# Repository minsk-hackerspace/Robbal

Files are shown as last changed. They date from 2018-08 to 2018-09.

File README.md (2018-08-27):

Robbal
===

Схемы, чертежи, инструкции по сборке робота балансира Rabbal

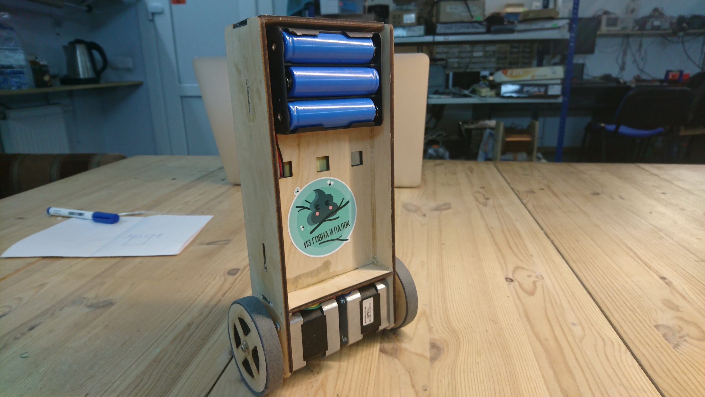
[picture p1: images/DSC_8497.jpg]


Робот баланси Robbal как отдельный [проект](https://hackerspace.by/projects/33) создается в рамках [курса](https://hackerspace.by/projects/31)

Купить готовый набор(конструктор) для сборки можно [в магазине Белчип](http://belchip.by/product/?selected_product=34442)

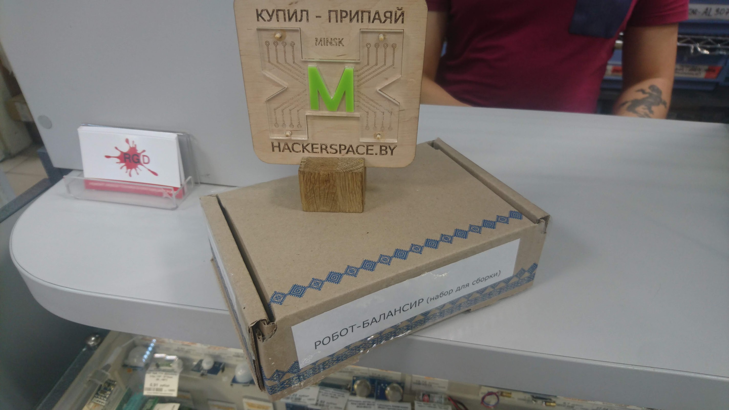
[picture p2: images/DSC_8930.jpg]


Основан на этом проекте [YABR](http://www.brokking.net/yabr_main.html)
Имеет более простую схему, а так-же управляется по блютусу с любого Android телефона.

Видео
---

ROBBAL (https://www.youtube.com/watch?v=0WFv116GKos)

Набор, Конструкция, Схема, Чертеж, Прошивка.
---

- [Комплектация набора](https://github.com/minsk-hackerspace/Robbal/blob/master/set.md)

- [Конструкция робота](https://github.com/minsk-hackerspace/Robbal/blob/master/design.md)

- [Схема робота](https://github.com/minsk-hackerspace/Robbal/blob/master/Robbal.png)

- [Чертеж корпуса](https://github.com/minsk-hackerspace/Robbal/blob/master/chassis.svg)

- [Скетч для Arduino](https://github.com/minsk-hackerspace/Robbal/blob/master/robbal/robbal.ino)

Инструкция по сборке:
---

- [блок питания](https://github.com/minsk-hackerspace/Robbal/blob/master/power.md)

- [шасси/корпус](https://github.com/minsk-hackerspace/Robbal/blob/master/chassis.md)

- [сборка схемы](https://github.com/minsk-hackerspace/Robbal/blob/master/assemble.md)

- [прошивка и нсатройка](https://github.com/minsk-hackerspace/Robbal/blob/master/tune.md)

- [найтройка bluetooth](https://github.com/minsk-hackerspace/Robbal/blob/master/bt.md)

- управление через android

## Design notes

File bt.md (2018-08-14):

Настройка bluetooth модуля HC-05
===

Управление роботом
---

Управление роботом осуществляется по bluetooth.
В качестве контроллера будет выступать любой Android смартфон с программой
Программа можете быть любая которая позволяет посылать настраиваеые команды на bloototh
В Play Market таких великое множество, например:

- [Arduino RC](https://play.google.com/store/apps/details?id=eu.jahnestacado.arduinorc)

- [Gadget Controller](https://play.google.com/store/apps/details?id=com.krio.gadgetcontroller)

Приемником управления будет выступать блютус модуль HC-05
Он позволит принять ваши команды управления из Андроид сматрфона и отдать их в ардуино робота.

Подключение для настройки
---

Блютус модуль в наборе поставляется в виде распространенного модуля HC-05 и переходной платки.
Платка позволяет втыкать его в макетку и питать от напряжения 5в (хотя логические уровни по прежнему остаются 3.3 вольта)
Так же на плате есть кнопка позволяющая перевести модуль в режим AT команд, зачем описано ниже.

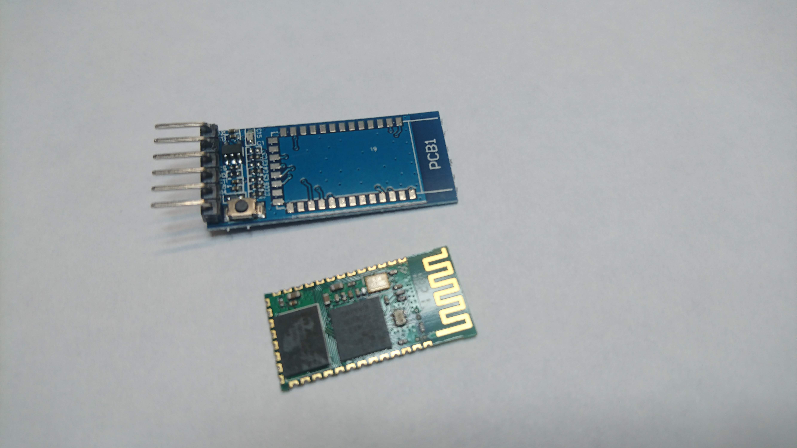
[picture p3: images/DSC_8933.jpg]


Модуль необходимо припапять на плату вот таким вот образом:
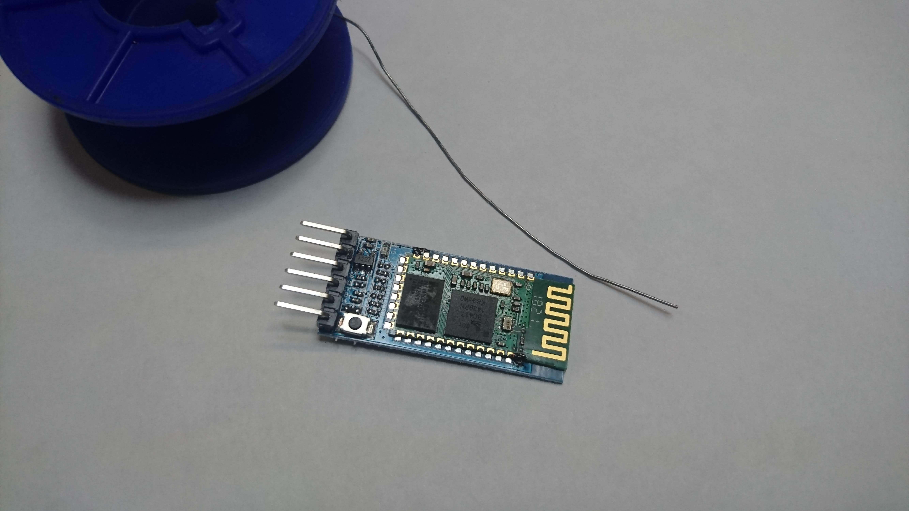
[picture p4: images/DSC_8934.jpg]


Должно получится что-то такое:
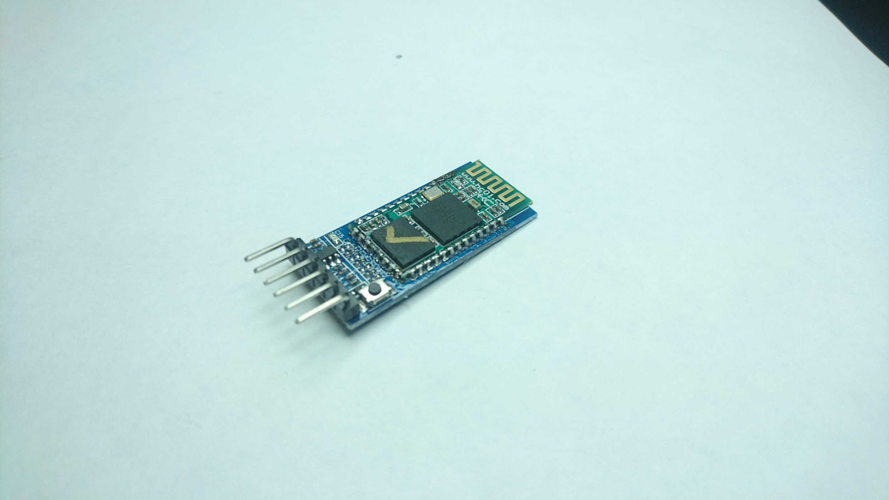
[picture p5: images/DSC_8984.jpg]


Далее необходимо настроить модуль под свои нужны. Все модули по дефолту имеют одинаковое имя и пароль, а так-же дефолтная скорость всего 9600 бод.

Для того чтобы настроить модуль, он подсоединяется через любой USB-UART переходник к компьютеру с Ardiono IDE. Важно джамперм или переключателем выставить напряжение UART 3.3 вольта.

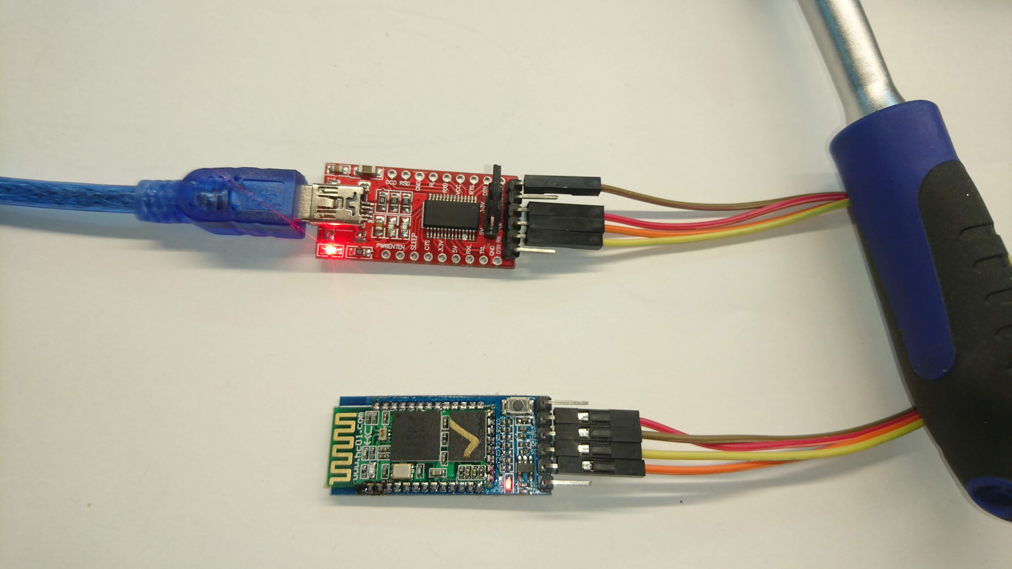
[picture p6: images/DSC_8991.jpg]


Подключение такое:

UART | HC-05
--- | ---
GND | GND
VCC | +5v
TX | RX
RX | TX

Настройка
---

Настройка происходит через Arduino IDE - Serial Monitor (Монитор порта) 
В строку ввода пишутся AT команды, а модуль как-то на них отвечает.
Чтобы зайти в AT режим необходимо подключать модуль с нажатой кнопкой на переходной платке.
В Serial Monitor необзодимо выставить скорость 38400 и перевод строки Both NL & CR (это стандартно для AT режима) 

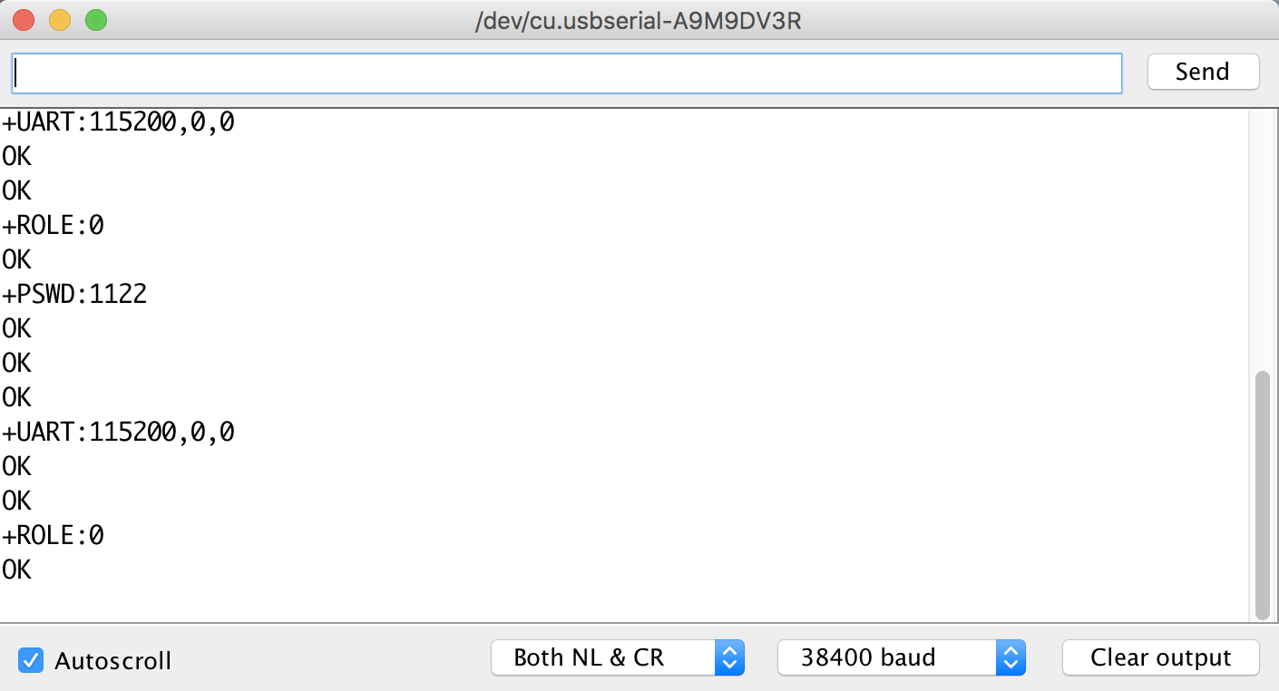
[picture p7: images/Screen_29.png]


Команда | Значение
--- | ---
AT | пустой запрос ответом должен быть OK
AT+NAME? | спросить имя модуля
AT+NAME=Robbal | задать имя модуля Robbal
AT+PSWD? | спросить пин код
AT+PSWD="1122" | Задать пин код 1122
AT+UART=115200,0,0 | Задать скорость уарт 115200 бод
AT+RESET | перезагрузка и выход из AT режима

Примерный листинг (лог) команд которым настраивается модуль с запросами и ответами.
```
> AT
< OK
> AT+NAME?
< +NAME:HC-05
> AT+NAME=Robbal
< OK
> AT+NAME?
< +NAME:Robbal
> AT+PSWD?
< +PIN:"1234"
> AT+PSWD="1122"
< OK
> AT+PSWD?
< +PIN:"1122"
> AT+ROLE?
< +ROLE:0
> AT+UART?
< +UART:9600,0,0
> AT+UART=115200,0,0
< OK
> AT+UART?
< +UART:115200,0,0
> AT+RESET
< OK
```

- [Полный мануал/даташит по модулю HC-05](http://www.electronicaestudio.com/docs/istd016A.pdf)

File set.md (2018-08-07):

Комплектация
===

[Набор](http://belchip.by/product/?selected_product=34442) для сборки из челчипа обладает минимальной комплектацией позволяющей собрать робота в хакерспейсе.

Название | модель/код | Количество
--- | --- | ---
Шаговый двигатель | 17HS2408 NEMA17 | 2	
Драйвер двигателя | Module DRV8825 | 2	
Аккумулятор 18650 | LIR18650 3.7V 2600mAh | 3	
Батарейный отсек | BH-3x18650 / 18650 x3 с проводами | 1	
Arduino Pro Mini | Модуль Atmega328 3В 8MHZ | 1
Модуль гироскопа | GY-521 MPU-6050 | 1
Модуль DC-DC | MP1584EN Mini | 1
Модуль Bluetooth | HC-05 Bluetooth Module | 1
Плата для Bluetooth | Base board for HC-05 | 1	

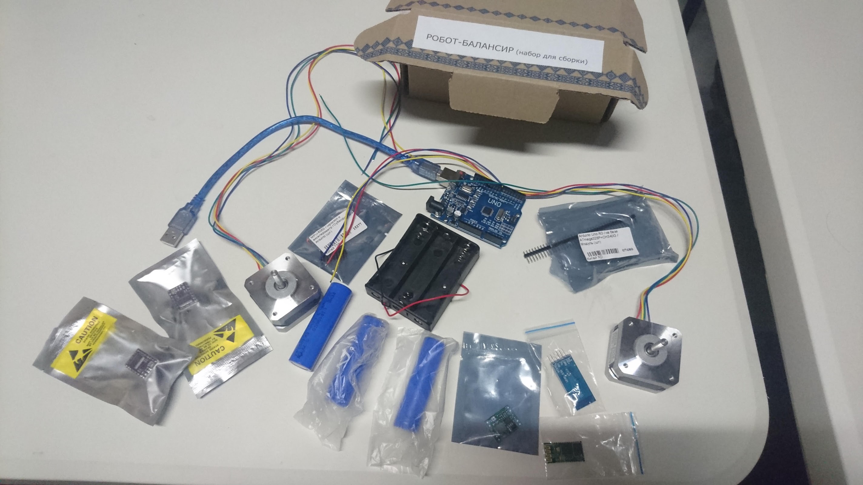
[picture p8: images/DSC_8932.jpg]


В комплект не входит необходимое для сборки и наладки:

- Переходник UART-USB для программирования Arduino 

- Зарядное устройство для аккумуляторов 18650

- Материал для корпуса / шасси / колес

Все это есть в хакерспейсе, но при самостоятельной сборке дома необходимо иметь ввиду.

Так же комплект можно расширить дополнительными деталями позволяющими расширить функциональность робота например:

- переключатель чтобы включать/выключать робота

- вольтметр чтобы отслеживать разряд батарей

- светодиодную ленту для подсветки

- сервопривод для механизма вставания

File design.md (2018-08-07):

Конструкция и дизайн робота
===

Робот разрабатывался для удовлетворения основных целей:

- простота конструкции и сборки

- минимальная и относительно дешевая комплектация

- широкие возможности для изменений/апгрейдов

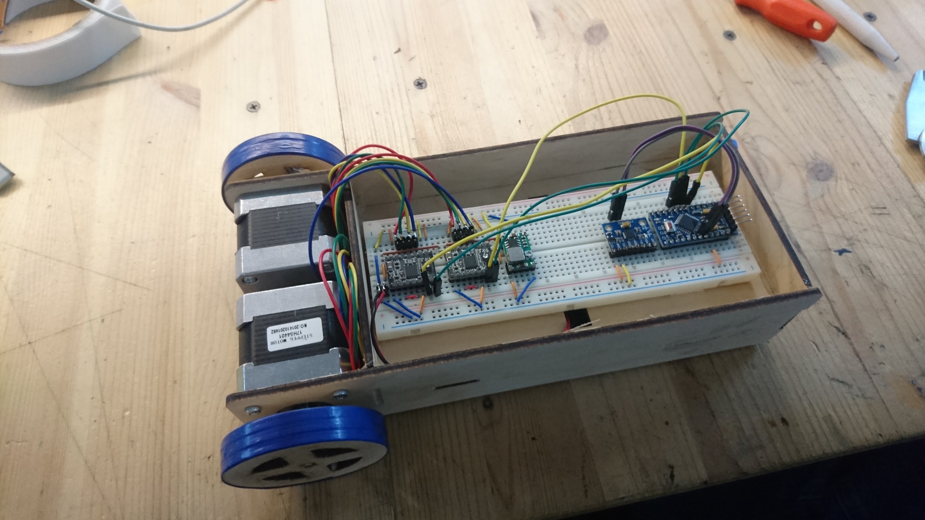
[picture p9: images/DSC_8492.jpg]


Физика и механка робота
---

В роботе вместо простых асинхронных используются более дорогие шаговые двигатели. Это обусловлено простотой настройки, высокой мощностью и точностью работы. Их не нужно будет согласовывать между собой, им не нужны редукторы, просто вставил и поехал. Можно использовать любые шаговики расчитанные на ток до 1.5 А. Корпус сделан под типоразмер NEMA17 но можно использовать более мощные NEMA23.

Корпус расчитан под лазерную резку минимального формата, но при этом позволяет разместить внутри стандартную макетную плату либо большую печатку размерами до 120х170. Так же копсус имеет два отдельных отсека что позволяет разместить схему и батарейки по разные стороны от оси, тем самым обеспечить более правильную балансировку по весу.

_При сборке робота для более качественной работы пид контроллера стоит размещать аккумуляторы в самой верхней части._

Конструкция робота позволяет менять ее в довольно широких пределах.
---

Есть несколько возможных вариантов сделать корпус, например:
- _корпус вырезанный из листового материала фанеры или акрила_ самый быстрый и проверенный способ. Раскрой для этого - [курпус в формате svg](https://rawgit.com/minsk-hackerspace/Robbal/master/chassis.svg). Необходимые размеры материала 30х40см, толщина 3-4мм
- _корпус напечатанный на 3д принтере_ самый сложный, долгий но самый крутой вариант. Необходимо самостоятельно моделировать и печатать корпус.

Есть несколько возможных вариантов собрать схему, например:

- _на контактной макетной плате_ самый быстрый, но самый ненадежный вариант детальки при падениях постоянно вываливаются. (макетка не входит в комплект)

- _паять на печатной макетке_  самый надежный но при этом самый трудоемкий вариант (печатка в комплект не входит)

- _навесной монтаж_ компромиссный вариант - просто проводками спаивать узлы между собой, затем на термоклей цеплять внутрь корпуса.

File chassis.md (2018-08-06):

ШАССИ
===

Шасси (корпус) вырезается лазером из фанеры (акрила) толщиной 3-4мм
Необходимая площадь листа для всех деталей корпуса 300х400мм

- [курпус в формате svg](https://rawgit.com/minsk-hackerspace/Robbal/master/chassis.svg)

- [курпус в формате dwg](https://rawgit.com/minsk-hackerspace/Robbal/master/chassis.dxf)

Нюансы
---
Пазы расчитаны под материал толщиной ровно 4 мм, поэтому если используется более тонкий матерал остаются щели, это нормально.

Внутренная полость достаточно большая (176х112 мм) чтобы туда поместилась стандартная беспаечная макетка, либо достаточно большая двухсторонная паечная макетка. 

Корпус сделан с минимальным клиренсом, так что при падении колеса поднимаются на пару миллиметров.

Колеса так же вырезаются из материала и на них натягивается колечко из резины (старая шина) Либо можно купить любые другие колеса для RC моделей диаметром 64-68 мм. Есть очень распространенные пластмассовые желтые и дешевые, ищутся по запросу "68mm robot wheel"

Сборка
---

Процесс сборки на фотках ниже.

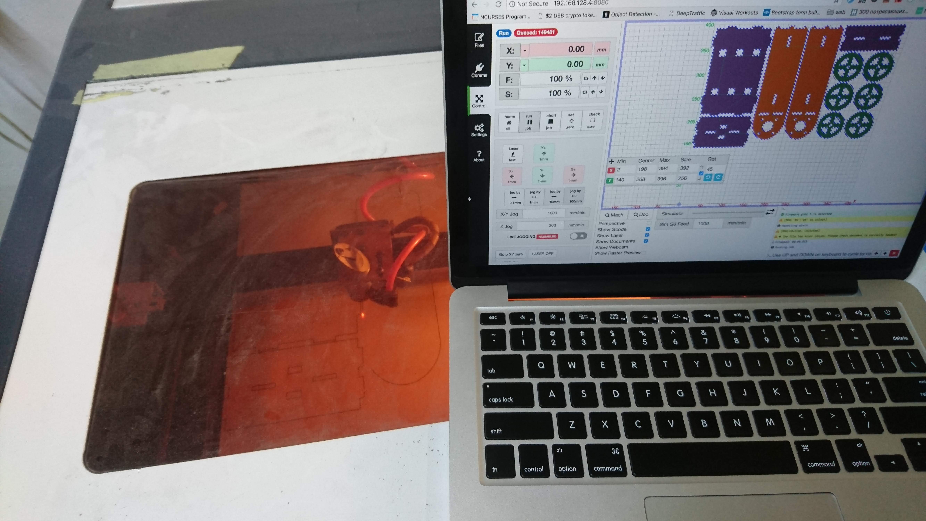
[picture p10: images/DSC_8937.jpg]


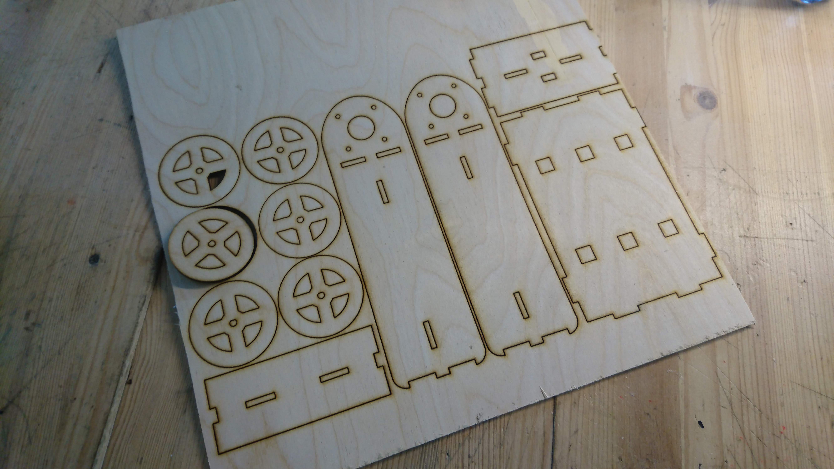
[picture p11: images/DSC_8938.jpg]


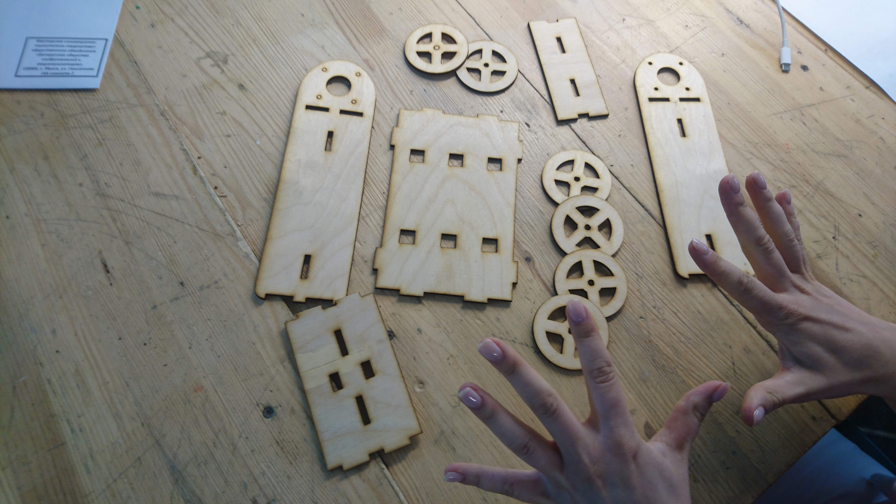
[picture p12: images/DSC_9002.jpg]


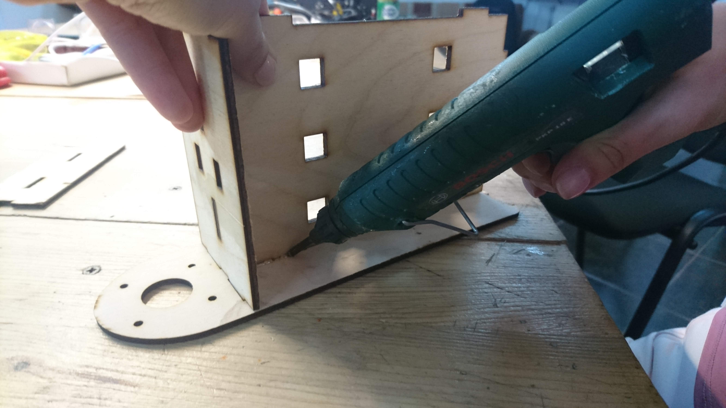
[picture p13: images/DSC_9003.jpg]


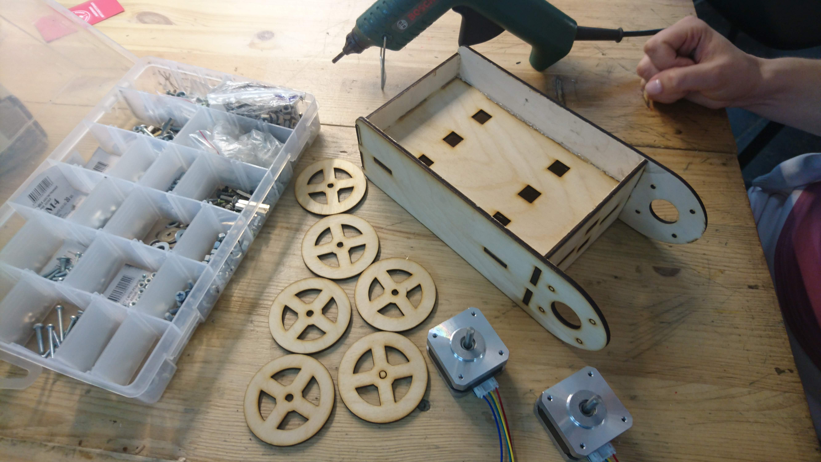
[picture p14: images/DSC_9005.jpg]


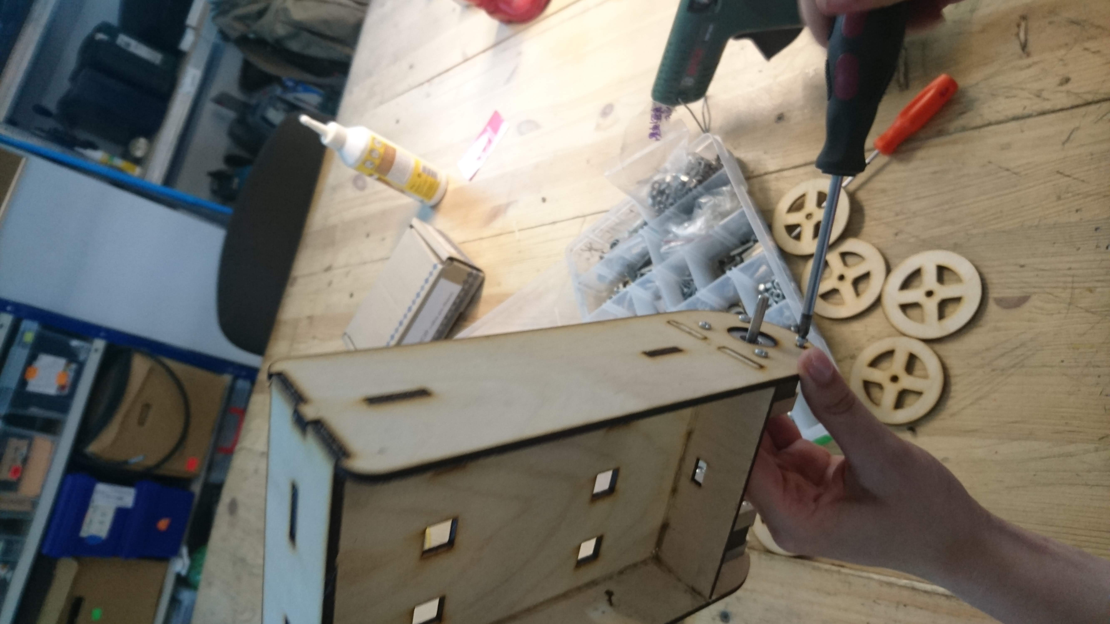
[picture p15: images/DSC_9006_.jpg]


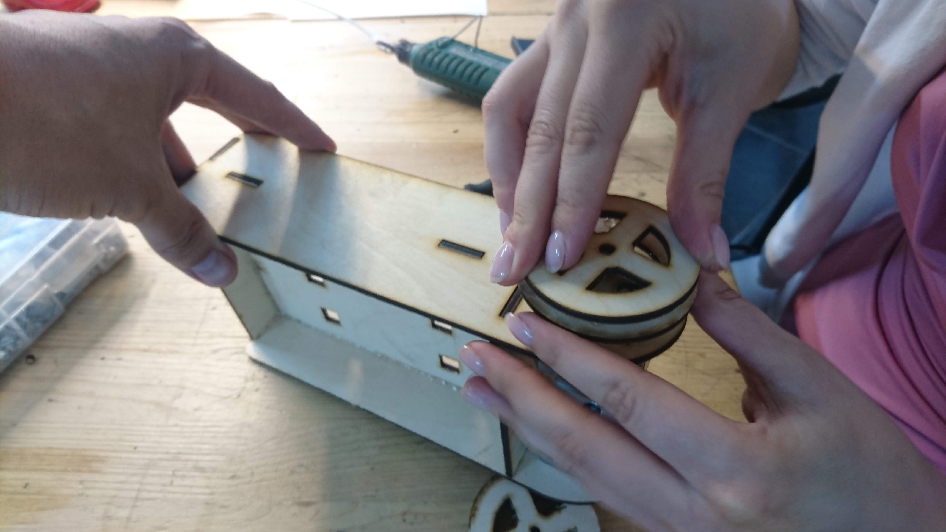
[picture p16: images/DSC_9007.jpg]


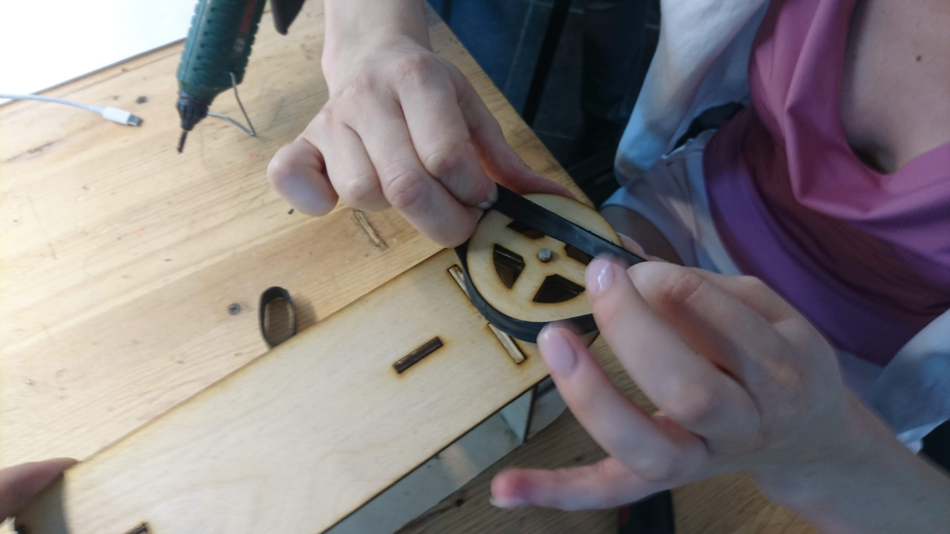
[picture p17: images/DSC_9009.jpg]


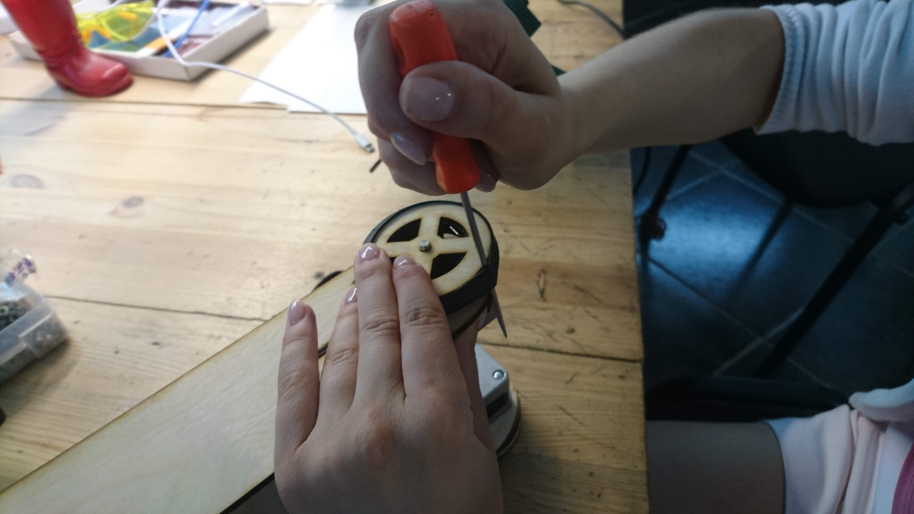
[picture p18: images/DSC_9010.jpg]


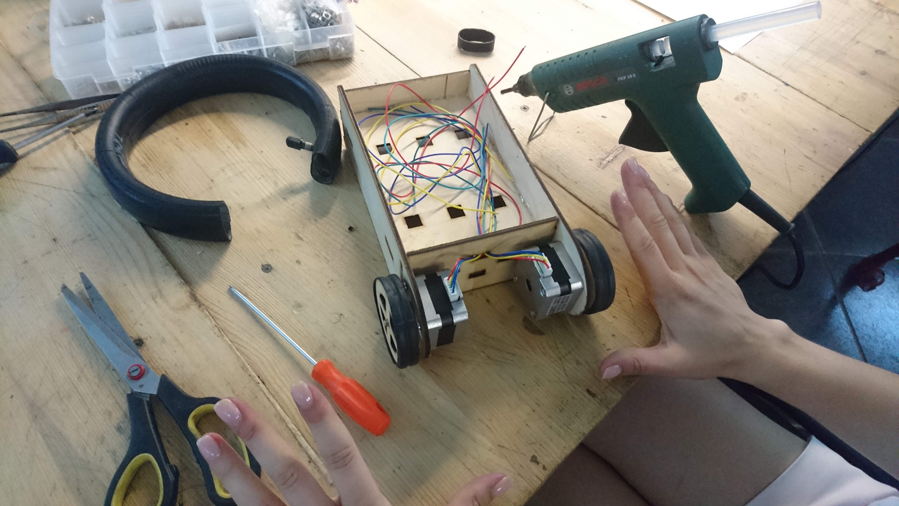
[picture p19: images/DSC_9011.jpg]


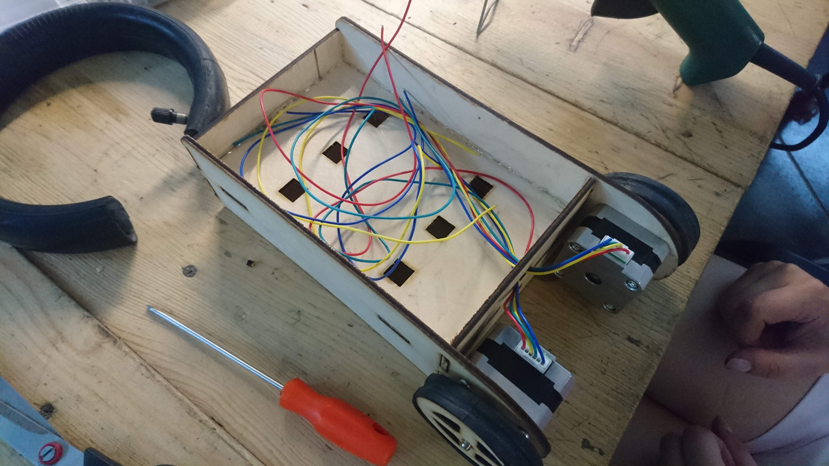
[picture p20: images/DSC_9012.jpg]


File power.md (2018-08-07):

Блок питания
===

Для питания роботу необходимы стабилизированные 3.3 вольта при токе до 100мА и нестабильные 9-24в с током до 1А для питания двигателей. Блок питания - это часть котоая будет выполнять эту функцию, состоит из:

- 3х Аккамулятор типоразмера 18650

- Акамуляторный отсек

- модуль преобразователя напряжения DC/DC 

Опционально в этот блок можно добавить выключатель и вольтметр.

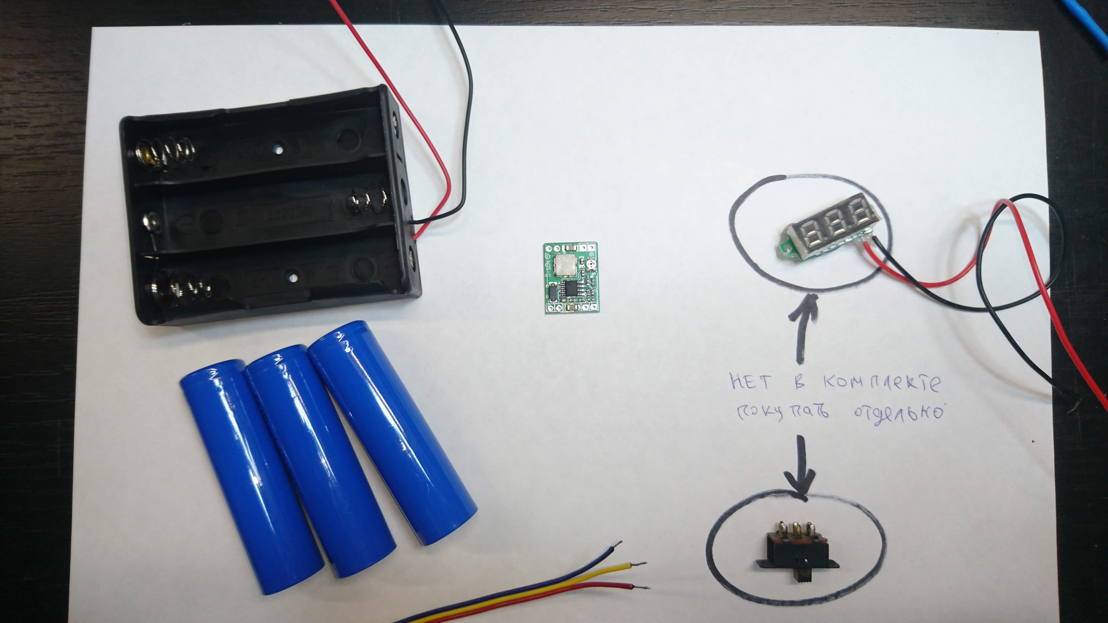
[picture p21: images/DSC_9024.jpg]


Схема
---

На общей схеме БП находится в левой верхней чертверти схемы.

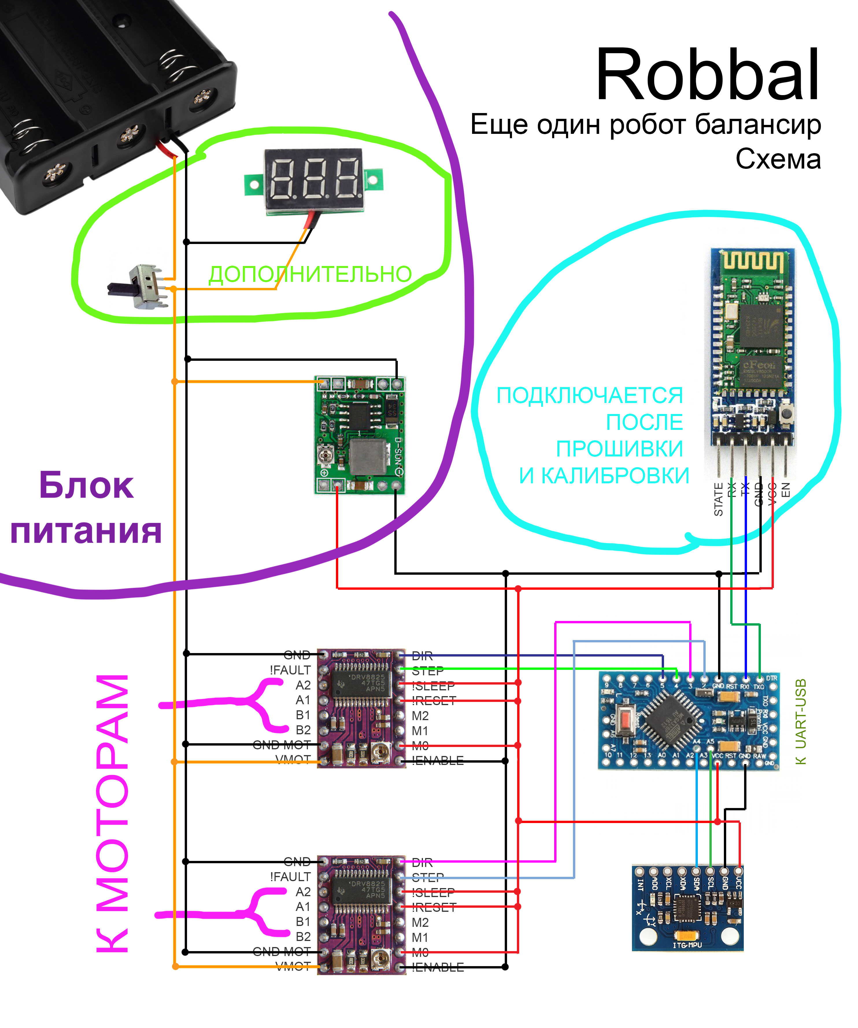
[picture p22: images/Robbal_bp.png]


Сборка
---

Фото процесса сборки: просто спайка проводами и крепление на термоклей

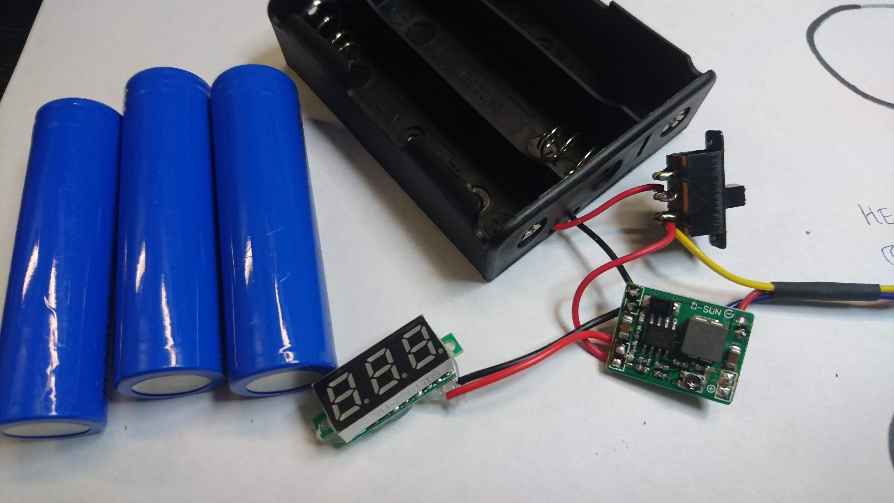
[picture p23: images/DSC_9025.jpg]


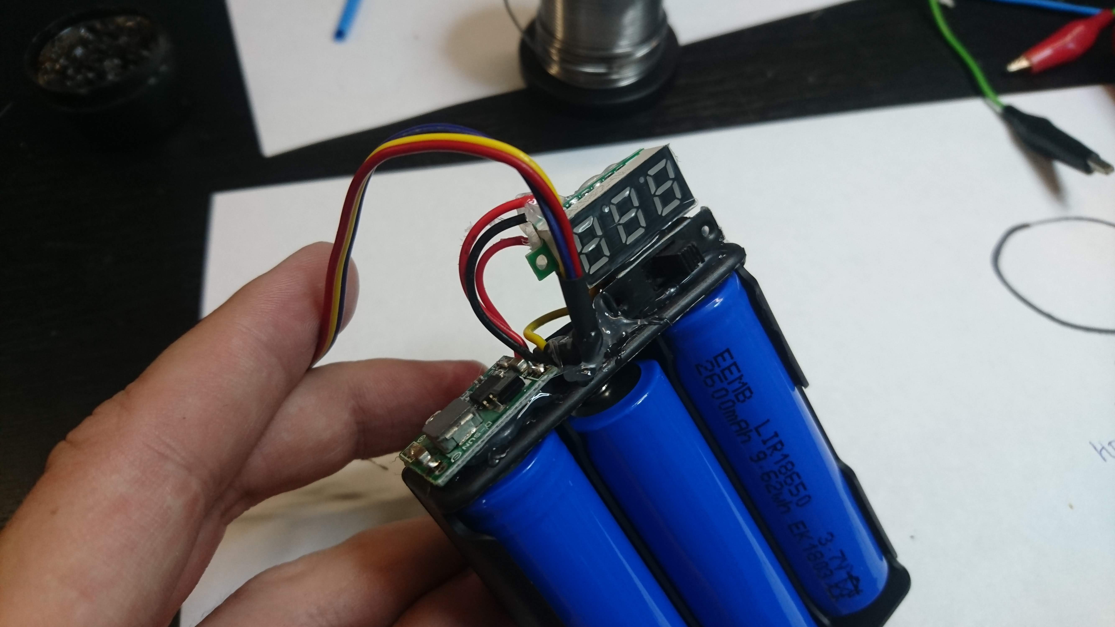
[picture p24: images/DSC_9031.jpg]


После сборки необходимо подкрутить подстроечный резистор на модуле DC/DC чтобы получить стабильное напряжение 3.3 В

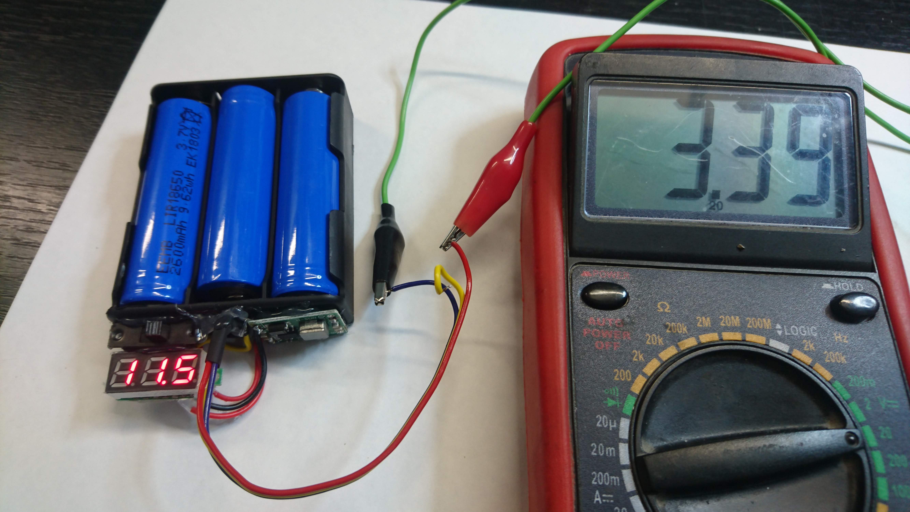
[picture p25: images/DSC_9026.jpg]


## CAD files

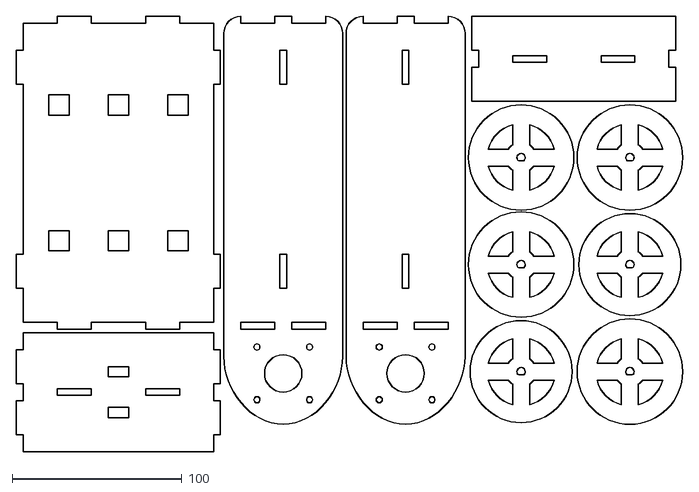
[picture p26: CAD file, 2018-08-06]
chassis.dxf
392.0 x 256.0

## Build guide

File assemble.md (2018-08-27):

СБОРКА СХЕМЫ
===

Схема условно делится на несколько частей:

* Блок питания 
* Основная схема 
* Блок управления



Схему можно собирать несколькими разными способами:

- Собрать на бесконтактной макетке

- Спаять на печатной макетной плате 

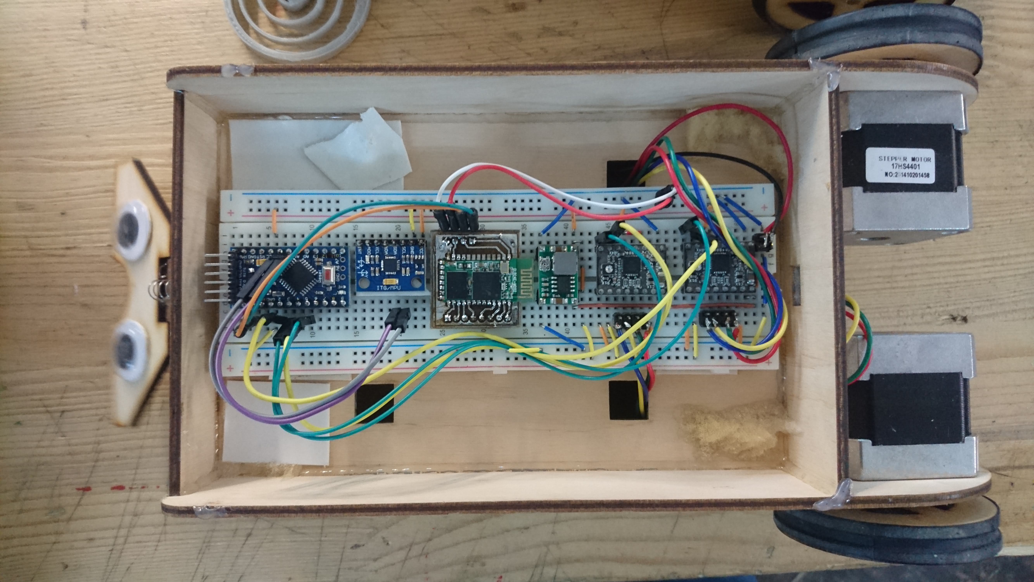
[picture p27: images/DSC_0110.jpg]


- Спаять модули проводами с некоторыми раззъемными соединениями

Сборка последним способом показанв на картинках ниже.

Сборка блока питания:
---

Блок питания это отсек с аккумуляторами и DC-DC преобразователь. Опционально можно добавить выключатель и модуль вольтметра чтобы видеть когда пора заряжать аккумуляторы. После спайки обязательно отрегулировать DC-DC модуль на стабилизированные +3.3В.
Так же сам DC-DC и дополнительные кнопку и вольтметр кремятся с помощью термопистолета на отсек.

В результате сборки блока питания зз него должно выходить три(четыре) провода:

- Нестабилизированные +11.7 В для питания двигателей. 
- Стабилизированные +3.3В для питания всей логики. 
- Земля одна или два провода.









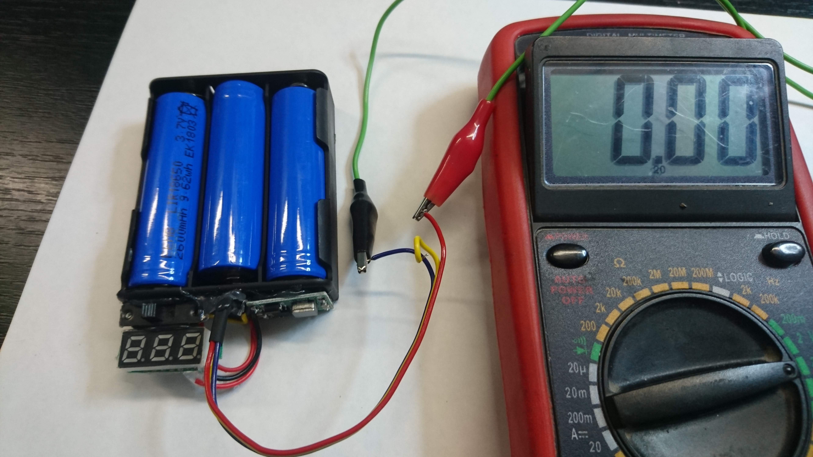
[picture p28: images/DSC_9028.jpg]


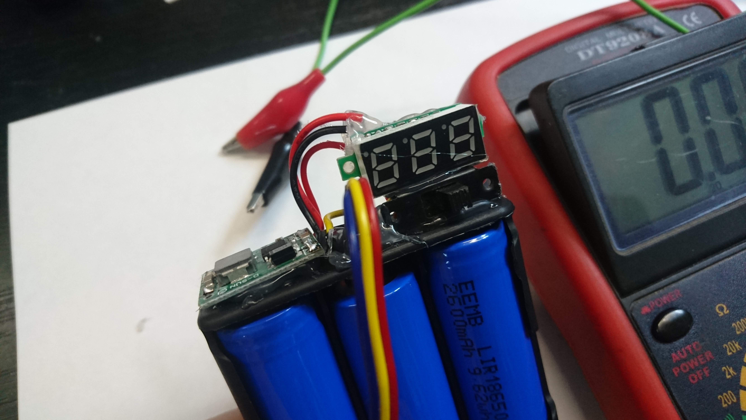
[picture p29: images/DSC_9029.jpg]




Сборка основной схемы:
---

Основная схема это соедененные проводами Ардуина, шаговые драйвера и гироскоп.
Соединяется все по схеме достаточно просто с помощью небольшого количества проводков.
Для удобства немлохо иметь коннекторы к шаговым двигателям и на питание всей схемы. 

Из нюансов стоит обратить внимание и правильно подсоединить к драйверам пары обмоток шагового двигателя. 
На фотографиях обмотки это синий+желтый и красный+зеленый.

Так же можно предусмотреть перемычки для настройки микростеппинга на драйверах. Хорошо себя показали 1/2 и 1/4 микрошага.
При 1/2 можно развить большую скорость. При 1/4 движения более плавные, робот легче в настройке и меньше падает.

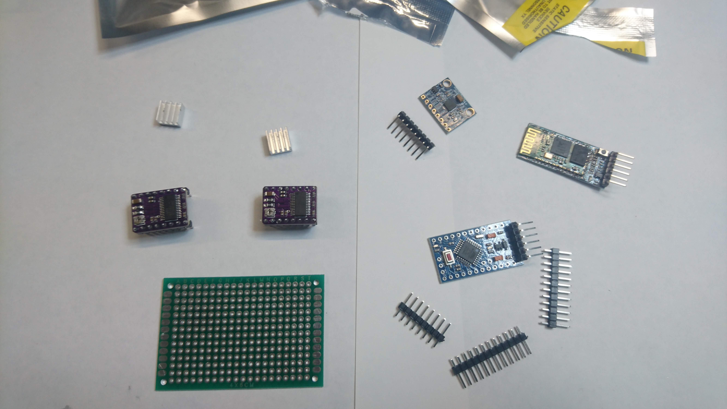
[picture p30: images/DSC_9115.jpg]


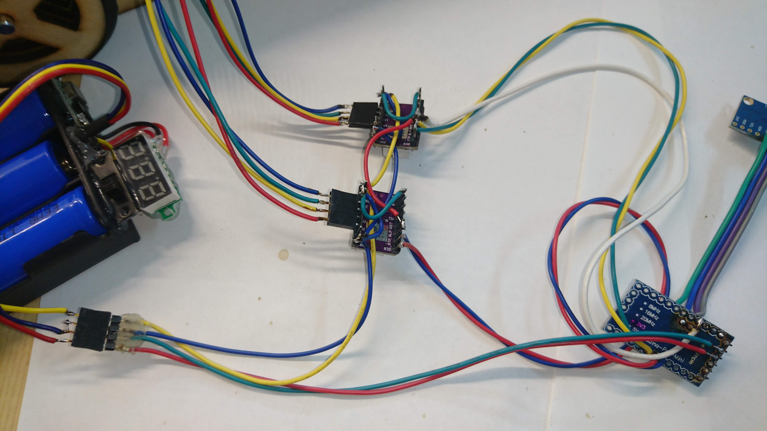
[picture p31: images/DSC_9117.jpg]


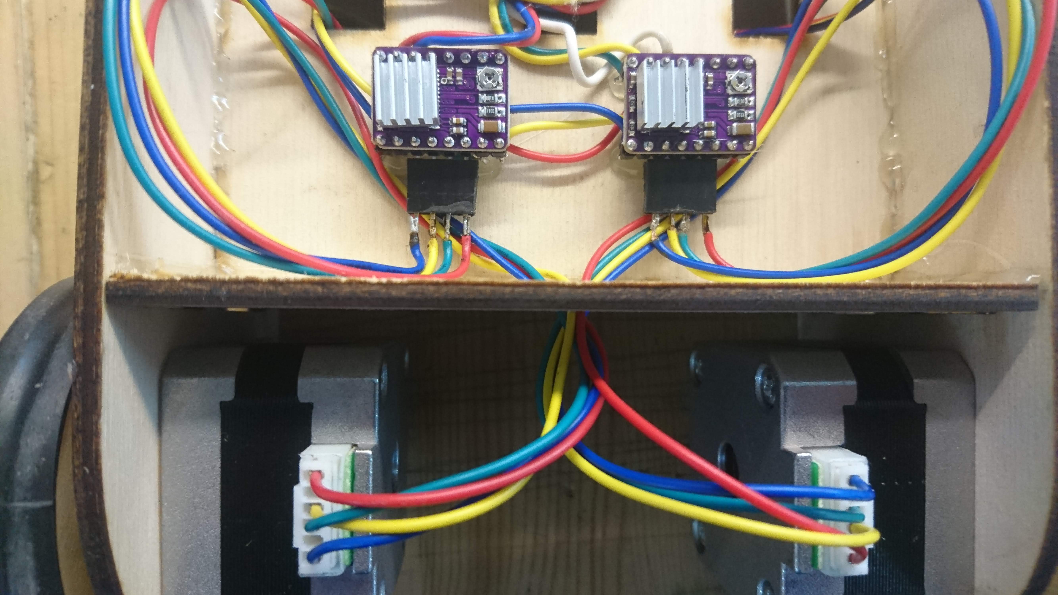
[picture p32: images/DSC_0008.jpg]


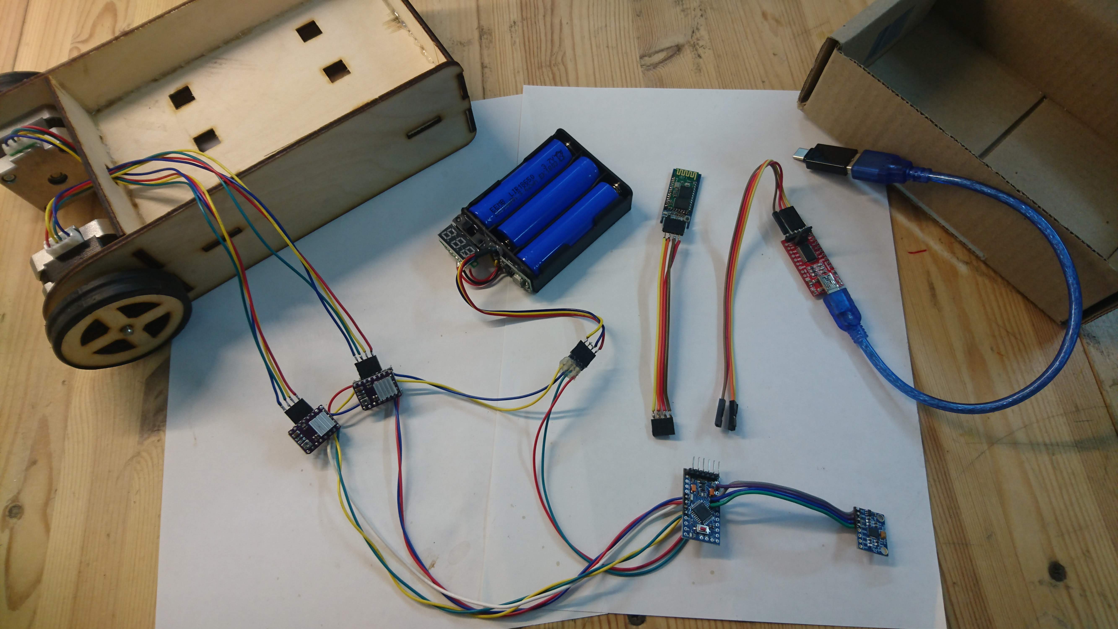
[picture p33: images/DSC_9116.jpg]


Сборка блока управления:
---

Блок управления - это модуль HC-05 распаяный на переходную платку. 
Так же удобно к нему иметь 4х жильный провод мама-мама чтобы подсоединять его напрямую к разъему на Arduino.
Подсоединяется он туда только после того [блютус модуль настроен](https://github.com/minsk-hackerspace/Robbal/blob/master/bt.md), а сама [схема откалибрована](https://github.com/minsk-hackerspace/Robbal/blob/master/tune.md)



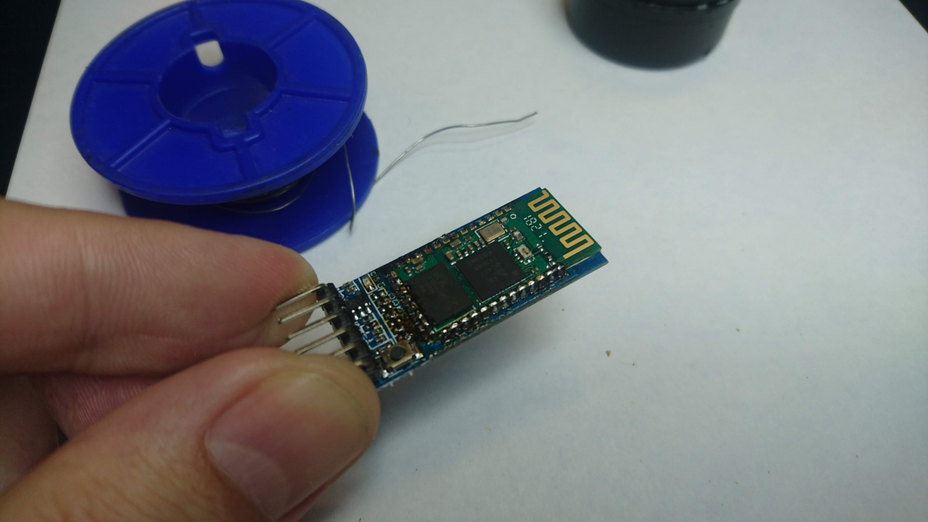
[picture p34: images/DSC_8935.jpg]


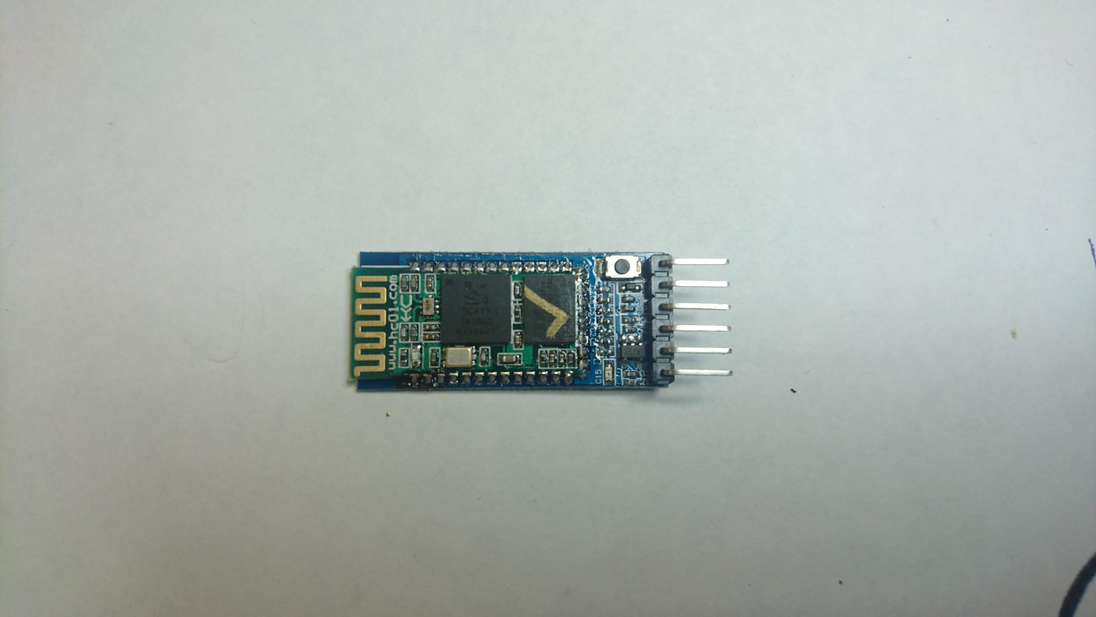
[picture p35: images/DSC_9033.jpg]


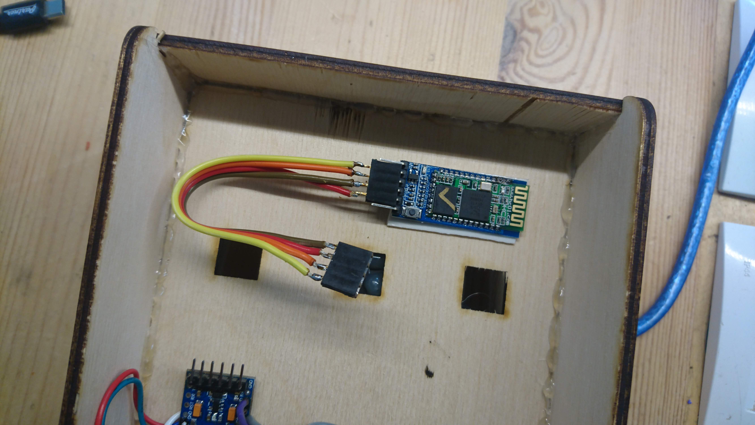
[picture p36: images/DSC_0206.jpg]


Крепление схемы в корпус
---
После спайки соединенные проводами модули крепится на термоклей внутрь корпуса.

*ВАЖНО* Разместить ось гироскопа таким образом чтобы версикальной была либо ось Y либо ось X. 
Маркировку осей можно увидеть на самом гироскопе.

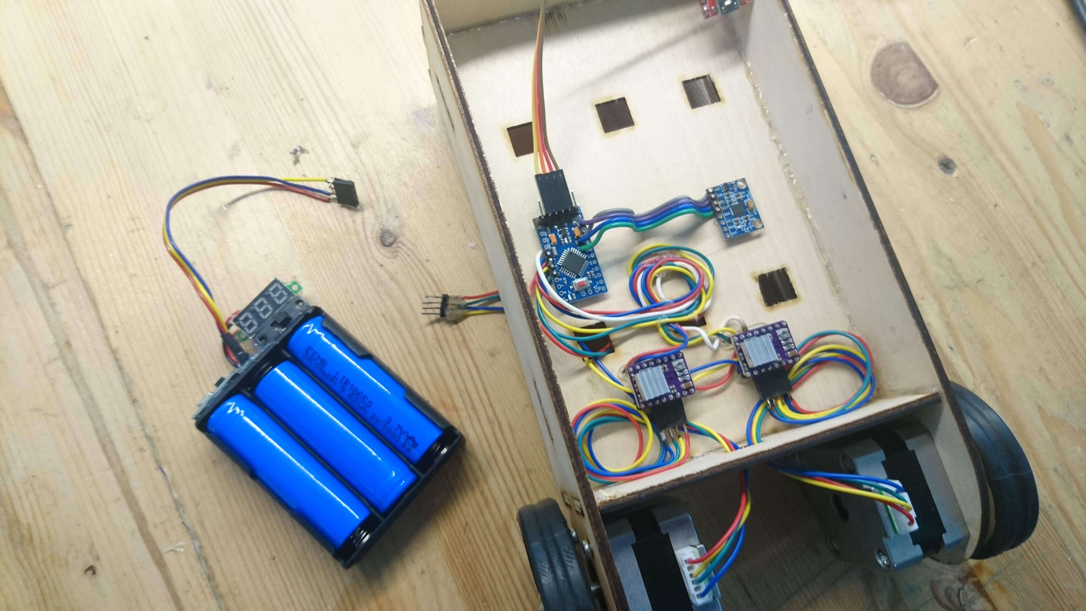
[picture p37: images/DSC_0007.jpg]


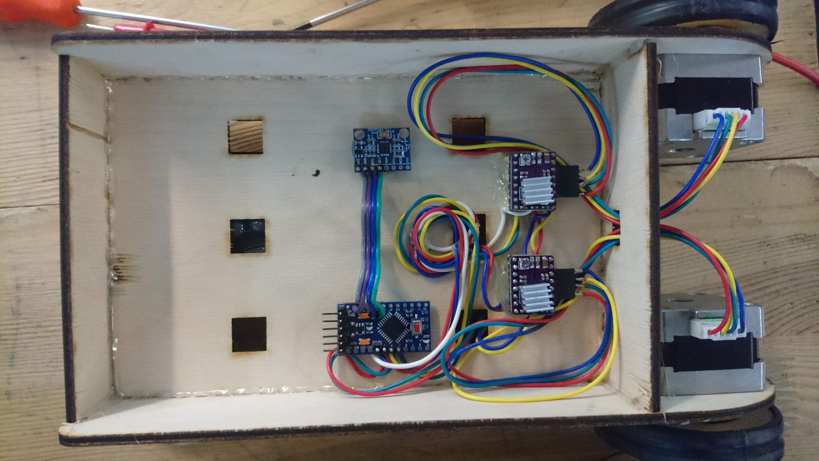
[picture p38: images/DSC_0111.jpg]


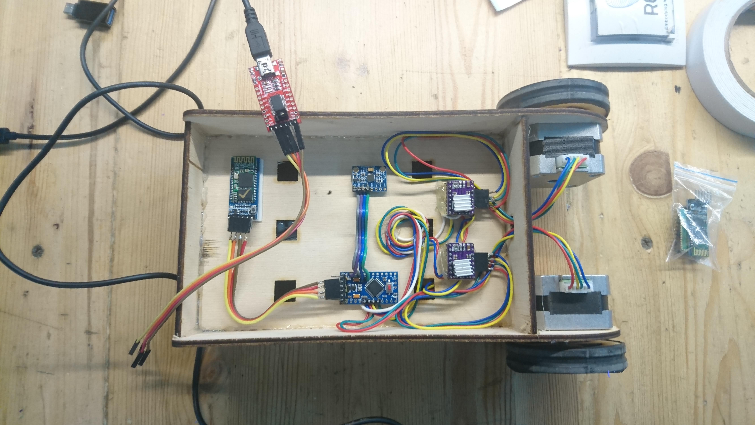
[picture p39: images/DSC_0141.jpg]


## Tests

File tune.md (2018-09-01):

Прошивка, настройка и калибровка.
===

Настройка драйверов.
---

Первым делом после сборки схемы необходимо выставить ограничение тока шаговых двигателей.
Это делается при первом включении. Проще всего это сделать при помощи измерения напряжения на подстроечном резисторе, которым собственно и ограничивается ток. Формула для драйвера DRV8825 такая: ``` Imax = 2 * Vref ```
Если используются шаговые двигатели с током обмоток 0.6А, то подстроечный резистор необходимо накрутить так, чтобы на нем было напряжение 0.3В

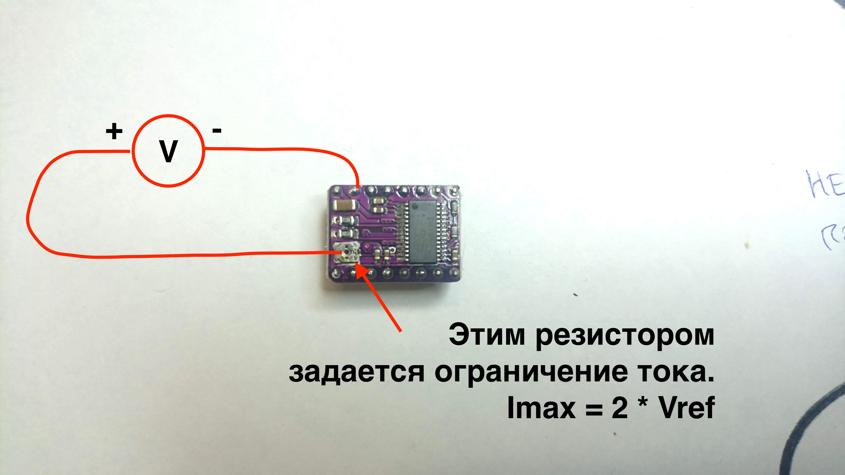
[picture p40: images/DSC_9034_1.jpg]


Более подробная стастья по настройке [тут](https://www.pololu.com/product/1182)

Прошивка.
---

В прошивке Arduino нет ничего необычного
Скачивается [скетч для Arduino](https://github.com/minsk-hackerspace/Robbal/blob/master/robbal/robbal.ino)
И прошивается самым [обычным способом](https://www.arduino.cc/en/Guide/ArduinoProMini), через UART переходник.

*Важно* Если в собранной конструкции робота вертикально расположена ось Y гироскопа в скетче должна присутствовать строчка
```#define flipXY``` 
Если вертикально расположена ось Х гироскопа то эту строчку следует закомментировать или убрать.

Бывает так что Arduino IDE не может прошить Arduino и отваливается с ошибкой "avrdude: stk500_getsync(): not in sync" Это распростаненная проблема когда есть проблемы с драйверами или UART или bootloader-ом в ардуине. Лечится кучей разных способов. Можно просто попробовать нажать кнопку reset на плате Arduino в момент начала прошивки. (нажать upload в Arduino IDE и через секунду reset на самой Arduino)

Прошивка работает таким образом:
При включении робот выводит в Serial ```hello balancing robot``` и начинает калибровку. ```Calibration...``` При этом робот должен лежать так, чтобы ось Z акселерометра была направлена вверх. Так проходит несколько секунд, за это время высчитваются дрейфы по осям X и Y, и робот быстро моргает светодиодом на ардуине. После калибровки в в Serial выводится ```Calibration Done``` робот моргает свтодиодом раз в секунду и ждет чтобы его подняли до почти вертикального положения. В вертикальном положении робот включается пишет ``` start ``` и подхватывает свой вес.

__ Serial порт работает на скорости 115200 бод. __

Калибровка вертикали (точки баланса)
---

После прошивки скетча рекомендуется отсоеденить моторы и выставить точку баланса.
Не всегда после сборки вертикальная ось получается строго вертикально. На это влиеет установка компонентов внутрь корпуса, их развесовка и даже распайка чипа на саму плату.

Для этого нужно отсоединить моторы и запустить робота с подключенным кабелеи UART и включенным Serial Monotir. После запуска, калибровки и старта В Serial Monitor время от времени робот реортит свой угол в двух значениях: сырые данные ```accelerometer_data_raw XXX``` и высчитаное значение в градусах ```angle X```

Поднимая робота так, чтобы он практически стоял под своим весом и никуда не отклонялся следим за выводимым значением ```accelerometer_data_raw XXX``` Затем в прошивке в значение ```acc_calibration_value``` необходимо выставить обратное значение и перепрошить робота.

Другими словами необходимо подобрать переменную ```acc_calibration_value``` таким образом чтобы при вертикальном положении значение ```accelerometer_data_raw``` было близко к нулю. Связяны эти значения по такой формуле ```  accelerometer_data_raw = accelerometer_data_read + acc_calibration_value; ``` где ```accelerometer_data_read``` это значение полученное с акселерометра а ```accelerometer_data_raw``` это значение используемое для расчетов, в абсолютно вертикальном положении там должен быть ноль.

Правильное подключение моторов.
---
При правильном подключении моторов они должны вращатся в ту же сторону куда наклоняется робот от вертикального положения и чем сильнее наклон тем быстрее вращение. Ничего сложного в этом нет и все должно работать практически сразу. Когда что-то работает не так - то есть наксолько симптомов и их решения:

- Моторы пищат, но не крутятся

В этом случае либо они не правильно подключены к драйверам, либо неправильно выставлен ток или микростеппинг.
Подключение должно быть парами проводов к парам выводам драйвера A и B. Обычно это синий+желтый и красный+сезеный.
Ток должен быть таким чобы не превышать максимально допустимый для моторов, но при этом не слишком малым чтобы мог вращать колеса с достаточным усилием. Микрошаг должен быть 1/4 1/2 иногда можно даже 1. Чем полнее шаг - тем быстрее могут крутиться колеса, но при этом падает плавность и при резких стартах могут начаться пропуски шагов.

- Моторы крутятся в разные стороны.

Необходимо на одном из моторов перевернуть обмотки А/Б

- Моторы крутятся не в ту сторону.

Необходимо поменять моторы местами.

- Моторы начинают крурутится только при наклоне в стороны, вместо наклона взад/перед.

Неправильно определены оси, ```#define flipXY``` в прошивке.

Калибровка PID
---

Колибровка PID регулятора это самое интересное. Кто лучше подберет значения PID тот победит.
[ПИД](https://en.wikipedia.org/wiki/PID_controller) это Пропорционально Интегрально Диференциальный. В нем эти три составляющие и соответственно три коэффициента.
Есть множество способов расчета этих коэффициентов, ниже описан только метод ручного подбора.

На англ.вики есть хорошая картинка илюстрирующая основной принцип и раскрывающая смысл калибровки.
![Image](https://upload.wikimedia.org/wikipedia/commons/3/33/PID_Compensation_Animated.gif)

Первым делом в прошивке выставляются нулевые коэффициенты I/D и плавно начиная от нуля поднимается P - пропорциональная часть.
Робот при наклоне должен начать гребсти колесам так чтобы не упасть. При малых значениях P скорости будет не достаточно чтобы сопротивлятся падению, при больших значениях робот будет быстро резко переезжать точку баланса и заваливатся в обратную сторону. Значение P нужно подобрать таким чтобы робот только начинал переезжать точку баланса, но не слишком сильно.

Затем плавно поднимается значение I оно должно оставатся малым (до 5 процентов от значения P) 
При этом должен начать раскачиваться вперед назад у точки баланса с плавно затухающей амплитудой раскачиваний.
Если амплитуда увеличивается и робот падает - значение I - слишком большое. 

Последним плавно повышается коэффициент D он должен сократить количество колебаний до того комента как робот поймает баланс.
В этот момент можно немного сбавить коэффициен P.

Всё калибровка завершена. Робот можно пихать в стороны и он не должен падать.

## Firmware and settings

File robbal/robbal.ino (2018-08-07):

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
#include <jled.h>  // https://github.com/jandelgado/jled
#include <Wire.h>                                            //Include the Wire.h library so we can communicate with the gyro

int gyro_address = 0x68;                                     //MPU-6050 I2C address (0x68 or 0x69)
int acc_calibration_value = -660;                            //Enter the accelerometer calibration value

//Various settings
float pid_p_gain = 30;                                       //Gain setting for the P-controller (15)
float pid_i_gain = 1.1;                                      //Gain setting for the I-controller (1.5)
float pid_d_gain = 30;                                       //Gain setting for the D-controller (30)
float turning_speed = 50;                                    //Turning speed (20)
float max_target_speed = 100;                                //Max target speed (100)

float max_fwd_speed = 6;
float max_back_speed = 4;                               


///////////////////////////////////////////////////////////////////////////////////////////////////////////////////////////////////////
//Declaring global variables
///////////////////////////////////////////////////////////////////////////////////////////////////////////////////////////////////////
byte start, received_byte, low_bat;

int left_motor, throttle_left_motor, throttle_counter_left_motor, throttle_left_motor_memory;
int right_motor, throttle_right_motor, throttle_counter_right_motor, throttle_right_motor_memory;
int battery_voltage;
int receive_counter;
int gyro_pitch_data_raw, gyro_yaw_data_raw, accelerometer_data_raw;

long gyro_yaw_calibration_value, gyro_pitch_calibration_value;

unsigned long loop_timer;

float angle_gyro, angle_acc, angle, self_balance_pid_setpoint;
float pid_error_temp, pid_i_mem, pid_setpoint, gyro_input, pid_output, pid_last_d_error;
float pid_output_left, pid_output_right;


#define flipXY


/*
 * 
 * SATUS LED
 * 
 */
 

JLed led = JLed(LED_BUILTIN);


///////////////////////////////////////////////////////////////////////////////////////////////////////////////////////////////////////
//Setup basic functions
///////////////////////////////////////////////////////////////////////////////////////////////////////////////////////////////////////
void setup(){
  Serial.begin(115200);                                                       //Start the serial port at 9600 kbps

  Serial.println("hello balancing robot");
  Wire.begin();                                                             //Start the I2C bus as master
  TWBR = 12;                                                                //Set the I2C clock speed to 400kHz

  //To create a variable pulse for controlling the stepper motors a timer is created that will execute a piece of code (subroutine) every 20us
  //This subroutine is called TIMER2_COMPA_vect
  TCCR2A = 0;                                                               //Make sure that the TCCR2A register is set to zero
  TCCR2B = 0;                                                               //Make sure that the TCCR2A register is set to zero
  TIMSK2 |= (1 << OCIE2A);                                                  //Set the interupt enable bit OCIE2A in the TIMSK2 register
  TCCR2B |= (1 << CS21);                                                    //Set the CS21 bit in the TCCRB register to set the prescaler to 8
  OCR2A = 39;                                                               //The compare register is set to 39 => 20us / (1s / (16.000.000MHz / 8)) - 1
  TCCR2A |= (1 << WGM21);                                                   //Set counter 2 to CTC (clear timer on compare) mode

  Serial.println("Calibration...");
  pinMode(LED_BUILTIN, OUTPUT);      
  
  led.Blink(10,200).Forever();
  
  //By default the MPU-6050 sleeps. So we have to wake it up.
  Wire.beginTransmission(gyro_address);                                     //Start communication with the address found during search.
  Wire.write(0x6B);                                                         //We want to write to the PWR_MGMT_1 register (6B hex)
  Wire.write(0x00);                                                         //Set the register bits as 00000000 to activate the gyro
  Wire.endTransmission();                                                   //End the transmission with the gyro.
  //Set the full scale of the gyro to +/- 250 degrees per second
  Wire.beginTransmission(gyro_address);                                     //Start communication with the address found during search.
  Wire.write(0x1B);                                                         //We want to write to the GYRO_CONFIG register (1B hex)
  Wire.write(0x00);                                                         //Set the register bits as 00000000 (250dps full scale)
  Wire.endTransmission();                                                   //End the transmission with the gyro
  //Set the full scale of the accelerometer to +/- 4g.
  Wire.beginTransmission(gyro_address);                                     //Start communication with the address found during search.
  Wire.write(0x1C);                                                         //We want to write to the ACCEL_CONFIG register (1A hex)
  Wire.write(0x08);                                                         //Set the register bits as 00001000 (+/- 4g full scale range)
  Wire.endTransmission();                                                   //End the transmission with the gyro
  //Set some filtering to improve the raw data.
  Wire.beginTransmission(gyro_address);                                     //Start communication with the address found during search
  Wire.write(0x1A);                                                         //We want to write to the CONFIG register (1A hex)
  Wire.write(0x03);                                                         //Set the register bits as 00000011 (Set Digital Low Pass Filter to ~43Hz)
  Wire.endTransmission();                                                   //End the transmission with the gyro 

  pinMode(2, OUTPUT); //pulse                                                      //Configure digital poort 2 as output
  pinMode(3, OUTPUT); //dir                                                      //Configure digital poort 3 as output
  pinMode(4, OUTPUT); //pulse                                                      //Configure digital poort 4 as output
  pinMode(5, OUTPUT); //dir                                                      //Configure digital poort 5 as output
  pinMode(13, OUTPUT);                                                      //Configure digital poort 6 as output

  for(receive_counter = 0; receive_counter < 500; receive_counter++){       //Create 500 loops
    //if(receive_counter % 15 == 0)digitalWrite(13, !digitalRead(13));        //Change the state of the LED every 15 loops to make the LED blink fast
    
    
    Wire.beginTransmission(gyro_address);                                   //Start communication with the gyro
    Wire.write(0x43);                                                       //Start reading the Who_am_I register 75h
    Wire.endTransmission();                                                 //End the transmission
    Wire.requestFrom(gyro_address, 4);                                      //Request 2 bytes from the gyro

#ifdef flipXY
    gyro_pitch_calibration_value += Wire.read()<<8|Wire.read();               //Combine the two bytes to make one integer
    gyro_yaw_calibration_value += Wire.read()<<8|Wire.read();             //Combine the two bytes to make one integer
#else
    gyro_yaw_calibration_value += Wire.read()<<8|Wire.read();               //Combine the two bytes to make one integer
    gyro_pitch_calibration_value += Wire.read()<<8|Wire.read();             //Combine the two bytes to make one integer
#endif

    delayMicroseconds(5000); //Wait for 5000 microseconds to simulate the main program loop time
    if(receive_counter % 30 == 0) {
      Serial.println(".");
    }
    
  }
  gyro_pitch_calibration_value /= 500;                                      //Divide the total value by 500 to get the avarage gyro offset
  gyro_yaw_calibration_value /= 500;                                        //Divide the total value by 500 to get the avarage gyro offset

  loop_timer = micros() + 4000;                                             //Set the loop_timer variable at the next end loop time
  
  Serial.println("Calibration Done");
  Serial.println(gyro_pitch_calibration_value);
  Serial.println(gyro_yaw_calibration_value);

  led.Blink(10,1000).Forever();
  
}

///////////////////////////////////////////////////////////////////////////////////////////////////////////////////////////////////////
//Main program loop
///////////////////////////////////////////////////////////////////////////////////////////////////////////////////////////////////////

int rp = 0;

void loop(){
  if(Serial.available()){                                                   //If there is serial data available
    received_byte = Serial.read();                                          //Load the received serial data in the received_byte variable
    Serial.write(received_byte);
    receive_counter = 0;                                                    //Reset the receive_counter variable
  }
  if(receive_counter <= 25)receive_counter ++;                              //The received byte will be valid for 25 program loops (100 milliseconds)
  else received_byte = 0x00;                                                //After 100 milliseconds the received byte is deleted
  
  //Load the battery voltage to the battery_voltage variable.
  //85 is the voltage compensation for the diode.
  //Resistor voltage divider => (3.3k + 3.3k)/2.2k = 2.5
  //12.5V equals ~5V @ Analog 0.
  //12.5V equals 1023 analogRead(0).
  //1250 / 1023 = 1.222.
  //The variable battery_voltage holds 1050 if the battery voltage is 10.5V.
  battery_voltage = (analogRead(0) * 1.222) + 85;
  battery_voltage = 1111;
  
  if(battery_voltage < 1050 && battery_voltage > 800){                      //If batteryvoltage is below 10.5V and higher than 8.0V
    //digitalWrite(13, HIGH);                                                 //Turn on the led if battery voltage is to low
    led.Blink(10,100).Forever();
    low_bat = 1;                                                            //Set the low_bat variable to 1
    Serial.print("battery_voltage ");
    Serial.println(battery_voltage);
    
  }

  ///////////////////////////////////////////////////////////////////////////////////////////////////////////////////////////////////////
  //Angle calculations
  ///////////////////////////////////////////////////////////////////////////////////////////////////////////////////////////////////////
  Wire.beginTransmission(gyro_address);                                     //Start communication with the gyro
  /*
   * 
   * 0x3B - ACCEL_XOUT_H
   * 0x3D - ACCEL_YOUT_H
   * 0x3F - ACCEL_ZOUT_H
   * 0x43 - GYRO_XOUT_H
   * 0x45 - GYRO_YOUT_H
   * 0x47 - GYRO_ZOUT_H
   * 
   */   
  Wire.write(0x3F);                                                         //Start reading at register 3F
  Wire.endTransmission();                                                   //End the transmission
  Wire.requestFrom(gyro_address, 2);                                        //Request 2 bytes from the gyro
  accelerometer_data_raw = Wire.read()<<8|Wire.read();                      //Combine the two bytes to make one integer
  accelerometer_data_raw += acc_calibration_value;                          //Add the accelerometer calibration value
  if(accelerometer_data_raw > 8200)accelerometer_data_raw = 8200;           //Prevent division by zero by limiting the acc data to +/-8200;
  if(accelerometer_data_raw < -8200)accelerometer_data_raw = -8200;         //Prevent division by zero by limiting the acc data to +/-8200;

  angle_acc = asin((float)accelerometer_data_raw/8200.0)* 57.296;           //Calculate the current angle according to the accelerometer

  
  if(start == 0 && angle_acc > -0.5&& angle_acc < 0.5){                     //If the accelerometer angle is almost 0

    Serial.print(" start ");
    led.Blink(10,2000).Forever();
    angle_gyro = angle_acc;                                                 //Load the accelerometer angle in the angle_gyro variable
    start = 1;                                                              //Set the start variable to start the PID controller
  }
  
  Wire.beginTransmission(gyro_address);                                     //Start communication with the gyro
  Wire.write(0x43);                                                         //Start reading at register 43
  Wire.endTransmission();                                                   //End the transmission
  Wire.requestFrom(gyro_address, 4);                                        //Request 4 bytes from the gyro

#ifdef flipXY  
  gyro_pitch_data_raw = Wire.read()<<8|Wire.read();                           //Combine the two bytes to make one integer
  gyro_yaw_data_raw = Wire.read()<<8|Wire.read();                         //Combine the two bytes to make one integer
#else
  gyro_yaw_data_raw = Wire.read()<<8|Wire.read();                           //Combine the two bytes to make one integer
  gyro_pitch_data_raw = Wire.read()<<8|Wire.read();                         //Combine the two bytes to make one integer
#endif  

  gyro_pitch_data_raw -= gyro_pitch_calibration_value;                      //Add the gyro calibration value
  angle_gyro += gyro_pitch_data_raw * 0.000031;                             //Calculate the traveled during this loop angle and add this to the angle_gyro variable
  
  ///////////////////////////////////////////////////////////////////////////////////////////////////////////////////////////////////////
  //MPU-6050 offset compensation
  ///////////////////////////////////////////////////////////////////////////////////////////////////////////////////////////////////////
  //Not every gyro is mounted 100% level with the axis of the robot. This can be cause by misalignments during manufacturing of the breakout board. 
  //As a result the robot will not rotate at the exact same spot and start to make larger and larger circles.
  //To compensate for this behavior a VERY SMALL angle compensation is needed when the robot is rotating.
  //Try 0.0000003 or -0.0000003 first to see if there is any improvement.

  gyro_yaw_data_raw -= gyro_yaw_calibration_value;                          //Add the gyro calibration value
  //Uncomment the following line to make the compensation active
  //angle_gyro -= gyro_yaw_data_raw * 0.0000003;                            //Compensate the gyro offset when the robot is rotating

  angle_gyro = angle_gyro * 0.9996 + angle_acc * 0.0004;                    //Correct the drift of the gyro angle with the accelerometer angle

  if (rp > 200) {
    Serial.print("accelerometer_data_raw ");
    Serial.println(accelerometer_data_raw);
    Serial.print("angle ");
    Serial.println(angle_gyro);
    rp = 0;
  } else {
    rp++;
  }
  
  
  ///////////////////////////////////////////////////////////////////////////////////////////////////////////////////////////////////////
  //PID controller calculations
  ///////////////////////////////////////////////////////////////////////////////////////////////////////////////////////////////////////
  //The balancing robot is angle driven. First the difference between the desired angel (setpoint) and actual angle (process value)
  //is calculated. The self_balance_pid_setpoint variable is automatically changed to make sure that the robot stays balanced all the time.
  //The (pid_setpoint - pid_output * 0.015) part functions as a brake function.
  pid_error_temp = angle_gyro - self_balance_pid_setpoint - pid_setpoint;
  if(pid_output > 10 || pid_output < -10)pid_error_temp += pid_output * 0.015 ;

  pid_i_mem += pid_i_gain * pid_error_temp;                                 //Calculate the I-controller value and add it to the pid_i_mem variable
  if(pid_i_mem > 400)pid_i_mem = 400;                                       //Limit the I-controller to the maximum controller output
  else if(pid_i_mem < -400)pid_i_mem = -400;
  //Calculate the PID output value
  pid_output = pid_p_gain * pid_error_temp + pid_i_mem + pid_d_gain * (pid_error_temp - pid_last_d_error);
  if(pid_output > 400)pid_output = 400;                                     //Limit the PI-controller to the maximum controller output
  else if(pid_output < -400)pid_output = -400;

  pid_last_d_error = pid_error_temp;                                        //Store the error for the next loop

  if(pid_output < 5 && pid_output > -5)pid_output = 0;                      //Create a dead-band to stop the motors when the robot is balanced

  if(angle_gyro > 30 || angle_gyro < -30 || start == 0 || low_bat == 1){    //If the robot tips over or the start variable is zero or the battery is empty
    pid_output = 0;                                                         //Set the PID controller output to 0 so the motors stop moving
    pid_i_mem = 0;                                                          //Reset the I-controller memory
    start = 0;                                                              //Set the start variable to 0
    self_balance_pid_setpoint = 0;                                          //Reset the self_balance_pid_setpoint variable
  }

  ///////////////////////////////////////////////////////////////////////////////////////////////////////////////////////////////////////
  //Control calculations
  ///////////////////////////////////////////////////////////////////////////////////////////////////////////////////////////////////////
  pid_output_left = pid_output;                                             //Copy the controller output to the pid_output_left variable for the left motor
  pid_output_right = pid_output;                                            //Copy the controller output to the pid_output_right variable for the right motor

  if(char(received_byte) == '<'){  
    Serial.println("<");
    //If the first bit of the receive byte is set change the left and right variable to turn the robot to the left
    pid_output_left += turning_speed;
    pid_output_right -= turning_speed;
  }
  if(char(received_byte) == '>'){ 
    Serial.println(">");
    //If the second bit of the receive byte is set change the left and right variable to turn the robot to the right
    pid_output_left -= turning_speed;                                       //Decrease the left motor speed
    pid_output_right += turning_speed;                                      //Increase the right motor speed
  }

  bool slowdown = true;
  if(char(received_byte) == '^'){    
    Serial.println("^");
    //If the third bit of the receive byte is set change the left and right variable to turn the robot to the right
    if(pid_setpoint > -max_fwd_speed) pid_setpoint -= 0.05;                            //Slowly change the setpoint angle so the robot starts leaning forewards
    if(pid_output > max_target_speed * -1)pid_setpoint -= 0.005;            //Slowly change the setpoint angle so the robot starts leaning forewards
    slowdown = false;
  }
  if(char(received_byte) == '_'){ 
    Serial.println("_");
    //If the forth bit of the receive byte is set change the left and right variable to turn the robot to the right
    if(pid_setpoint < max_back_speed)pid_setpoint += 0.05;                             //Slowly change the setpoint angle so the robot starts leaning backwards
    if(pid_output < max_target_speed)pid_setpoint += 0.005;                 //Slowly change the setpoint angle so the robot starts leaning backwards
    slowdown = false;
  }   
  //left down
  if(char(received_byte) == '('){ 
    Serial.println("(");
    pid_output_left += turning_speed;
    pid_output_right -= turning_speed;
    if(pid_setpoint < max_back_speed) pid_setpoint += 0.05;
    if(pid_output < max_target_speed) pid_setpoint += 0.005;
    slowdown = false;
  }  
  //right down
  if(char(received_byte) == ')'){ 
    Serial.println(")");
    pid_output_left -= turning_speed;
    pid_output_right += turning_speed;
    if(pid_setpoint < max_back_speed) pid_setpoint += 0.05;
    if(pid_output < max_target_speed)pid_setpoint += 0.005;
    slowdown = false;
  }  
  //left up
  if(char(received_byte) == '{'){ 
    Serial.println("}");
    pid_output_left += turning_speed;
    pid_output_right -= turning_speed;
    if(pid_setpoint > -max_fwd_speed) pid_setpoint -= 0.05;
    if(pid_output > max_target_speed * -1)pid_setpoint -= 0.005;
    slowdown = false;
  }  
  //right up
  if(char(received_byte) == '}'){ 
    Serial.println("}");
    pid_output_left -= turning_speed;
    pid_output_right += turning_speed;
    if(pid_setpoint > -max_fwd_speed) pid_setpoint -= 0.05;
    if(pid_output > max_target_speed * -1)pid_setpoint -= 0.005;
    slowdown = false;
  }
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

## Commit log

2018-08-27 Add some new assemble photos
2018-08-27 Add assemble
